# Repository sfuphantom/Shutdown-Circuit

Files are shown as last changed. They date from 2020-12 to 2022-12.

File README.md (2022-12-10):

# Shutdown-Circuit
The Shutdown Circuit (SDC), now more commonly known as the high voltage (HV) and low voltage (LV) shutdown boards (SDBs), controls shutting down the vehicle in the occurance of a fault. Accordingly, the HV SDB is located in the HV system, and the LV SDB is in the LV system where if a fault were detected in either system then the vehicle turns off completely.

We use JLC PCB for supplying great PCBs in a timely manner:
https://jlcpcb.com/?from=RAT

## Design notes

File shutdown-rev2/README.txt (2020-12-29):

Additional Altium libraries required:

\Phantom-Library\LEDs.SchLib        # for LEDs
\Phantom-Library\Diodes.SchLib      # for diodes
\Phantom-Library\Misc.SchLib        # for testpoints
\Phantom-Library\Connectors.SchLib  # for 1x8 connector
\Phantom-Library\PCBLib             # for all generic footprints (resistors, capacitors, SOT23-3, etc.)

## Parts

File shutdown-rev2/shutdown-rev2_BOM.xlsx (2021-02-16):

Description | Designator | LibRef | Quantity
CAP CER 0.1UF 50V X7R 0603 | C1, C2, C3, C4, C5, C6, C7, C8, C9, C10, C11 | CL10B104KB8NNNL | 11
CAP CER 15UF 6.3V X5R 0603 | C12 | C1608X5R0J156M080AC | 1
LED YELLOW CLEAR 0603 SMD | D1 | LED-Yellow | 1
DIODE GEN PURP 600V 5A SMB | D2, D4, D6, D8 | Diode-600V-5A | 4
LED RED CLEAR 0603 SMD | D3, D5, D7, D9 | LED-Red-Bright | 4
CONN HEADER VERT 2POS 2.54MM | JP1, JP2, JP3, JP4 | 2PIN-TEST | 4
General Purpose Relay, Osa Series, Power, Non Latching, Dpst-No, 12 Vdc, 3 A Rohs Compliant: Yes | K1, K2, K3, K4 | 5-1419124-6 | 4
CONN HEADER VERT 2POS 5.7MM, 12-16AWG | M1 | 2002411112 | 1
4 PIN HDR, 3MM PITCH, 18-30 AWG | M2, M4 | 0436500428 | 2
CONN HEADER VERT 5POS 3MM | M3 | 0436500528 | 1
CONN HEADER R/A 8POS 2.54MM | M5 | 8PIN | 1
MOSFET 2N-CH 60V 0.25A SOT363 | Q1, Q3, Q5, Q7 | DMN63D1LDW | 4
P Channel MOSFET, -130 mA, -50 V, 1.2 ohm, -5 V, -1.7 V | Q2, Q4, Q6, Q8 | BSS84 | 4
MOSFET N-CH 50V 200MA SOT-23 | Q9 | BSS138LT3G | 1
RES SMD 240 OHM 5% 1/4W 0603 | R1, R3, R5, R8, R10 | ESR03EZPJ241 | 5
RES SMD 10K OHM 1% 1/10W 0603 | R2, R4, R9, R11, R16 | CRCW060310K0FKEA | 5
RES SMD 1K OHM 1% 1/10W 0603, RES SMD 240 OHM 5% 1/4W 0603 | R6, R7, R12, R17, R25 | CRCW06031K00FKEA, ESR03EZPJ241 | 5
RES 3K OHM 5% 1/10W 0603 | R13, R15, R20 | RMCF0603JT3K00 | 3
RES 9.1K OHM 1% 1/10W 0603 | R14, R18 | RMCF0603FT9K10 | 2
RES 7.5K OHM 1% 1/8W 0603 | R19 | RNCP0603FTD7K50 | 1
RES SMD 1.3K OHM 1% 1/8W 0603 | R21 | MCT06030C1301FP500 | 1
RES SMD 2.2K OHM 1% 1/10W 0603 | R22 | RC0603FR-072K2L | 1
RES SMD 33K OHM 1% 1/10W 0603 | R23 | RC0603FR-0733KL | 1
RES SMD 499 OHM 0.1% 1/10W 0603 | R24 | ERA-3AEB4990V | 1
RES SMD 2K OHM 0.1% 1/10W 0603 | R26 | ERA-3AEB202V | 1
Single layer pad TP | TP1, TP2, TP3 | Testpoint2 | 3
TVS DIODE ARRAY 12VWM SOT23-3 | U1, U4 | AQ12-02HTG | 2
TVS DIODE 5V 14.5V SOD323 | U2 | AQ05C-01FTG | 1
TVS DIODE ARRAY 5VWM SOT23-3 | U3, U6 | AQ05-02HTG | 2
TVS DIODE 12V 23V SOD323 | U5, U7 | AQ12C-01FTG | 2
IC COMPAR PWR RRI DL PP 8VSSOP | U8, U14 | TLV3202AIDGK | 2
IC GATE OR 2CH 2-INP US8 | U9 | NL27WZ32USGOSCT-ND | 1
Dual 2-Input Positive-AND Gate | U10 | SN74LVC2G08DCUT | 1
The SN74AHC1G04 contains one inverter gate. The device performs the Boolean function Y = A bar. | U11, U13 | SN74AHC1G04DCK | 2
Comparator Single R-R I/P 5.5V 5-Pin SC-70 T/R | U12 | TLV3201AIDCKR | 1

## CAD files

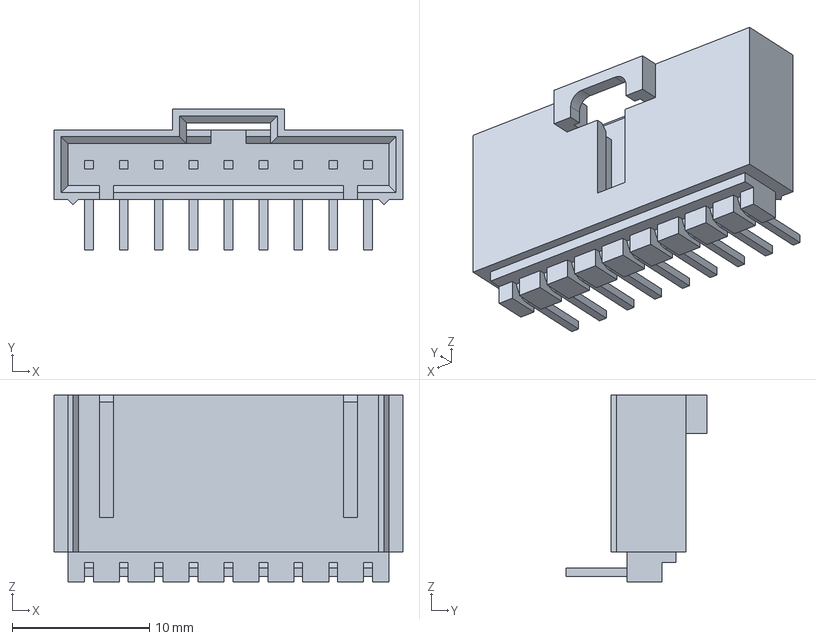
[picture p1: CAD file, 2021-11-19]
HV SDB/705530113.stp
25.4 x 10.3 x 13.6 mm

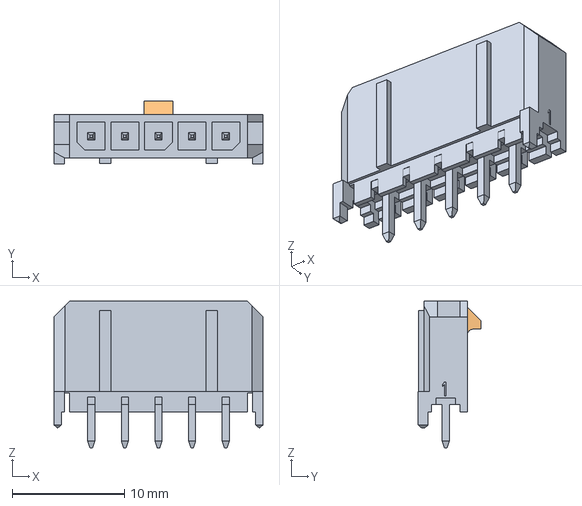
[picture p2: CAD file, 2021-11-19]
LV SDB/436500528.stp
18.6 x 5.61 x 13.1 mm

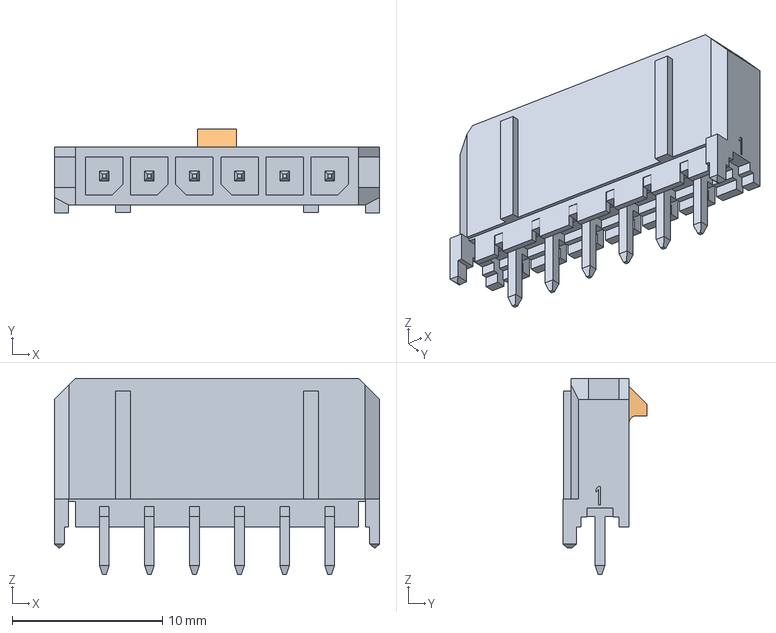
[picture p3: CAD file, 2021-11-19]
LV SDB/436500628.stp
21.6 x 5.61 x 13.1 mm

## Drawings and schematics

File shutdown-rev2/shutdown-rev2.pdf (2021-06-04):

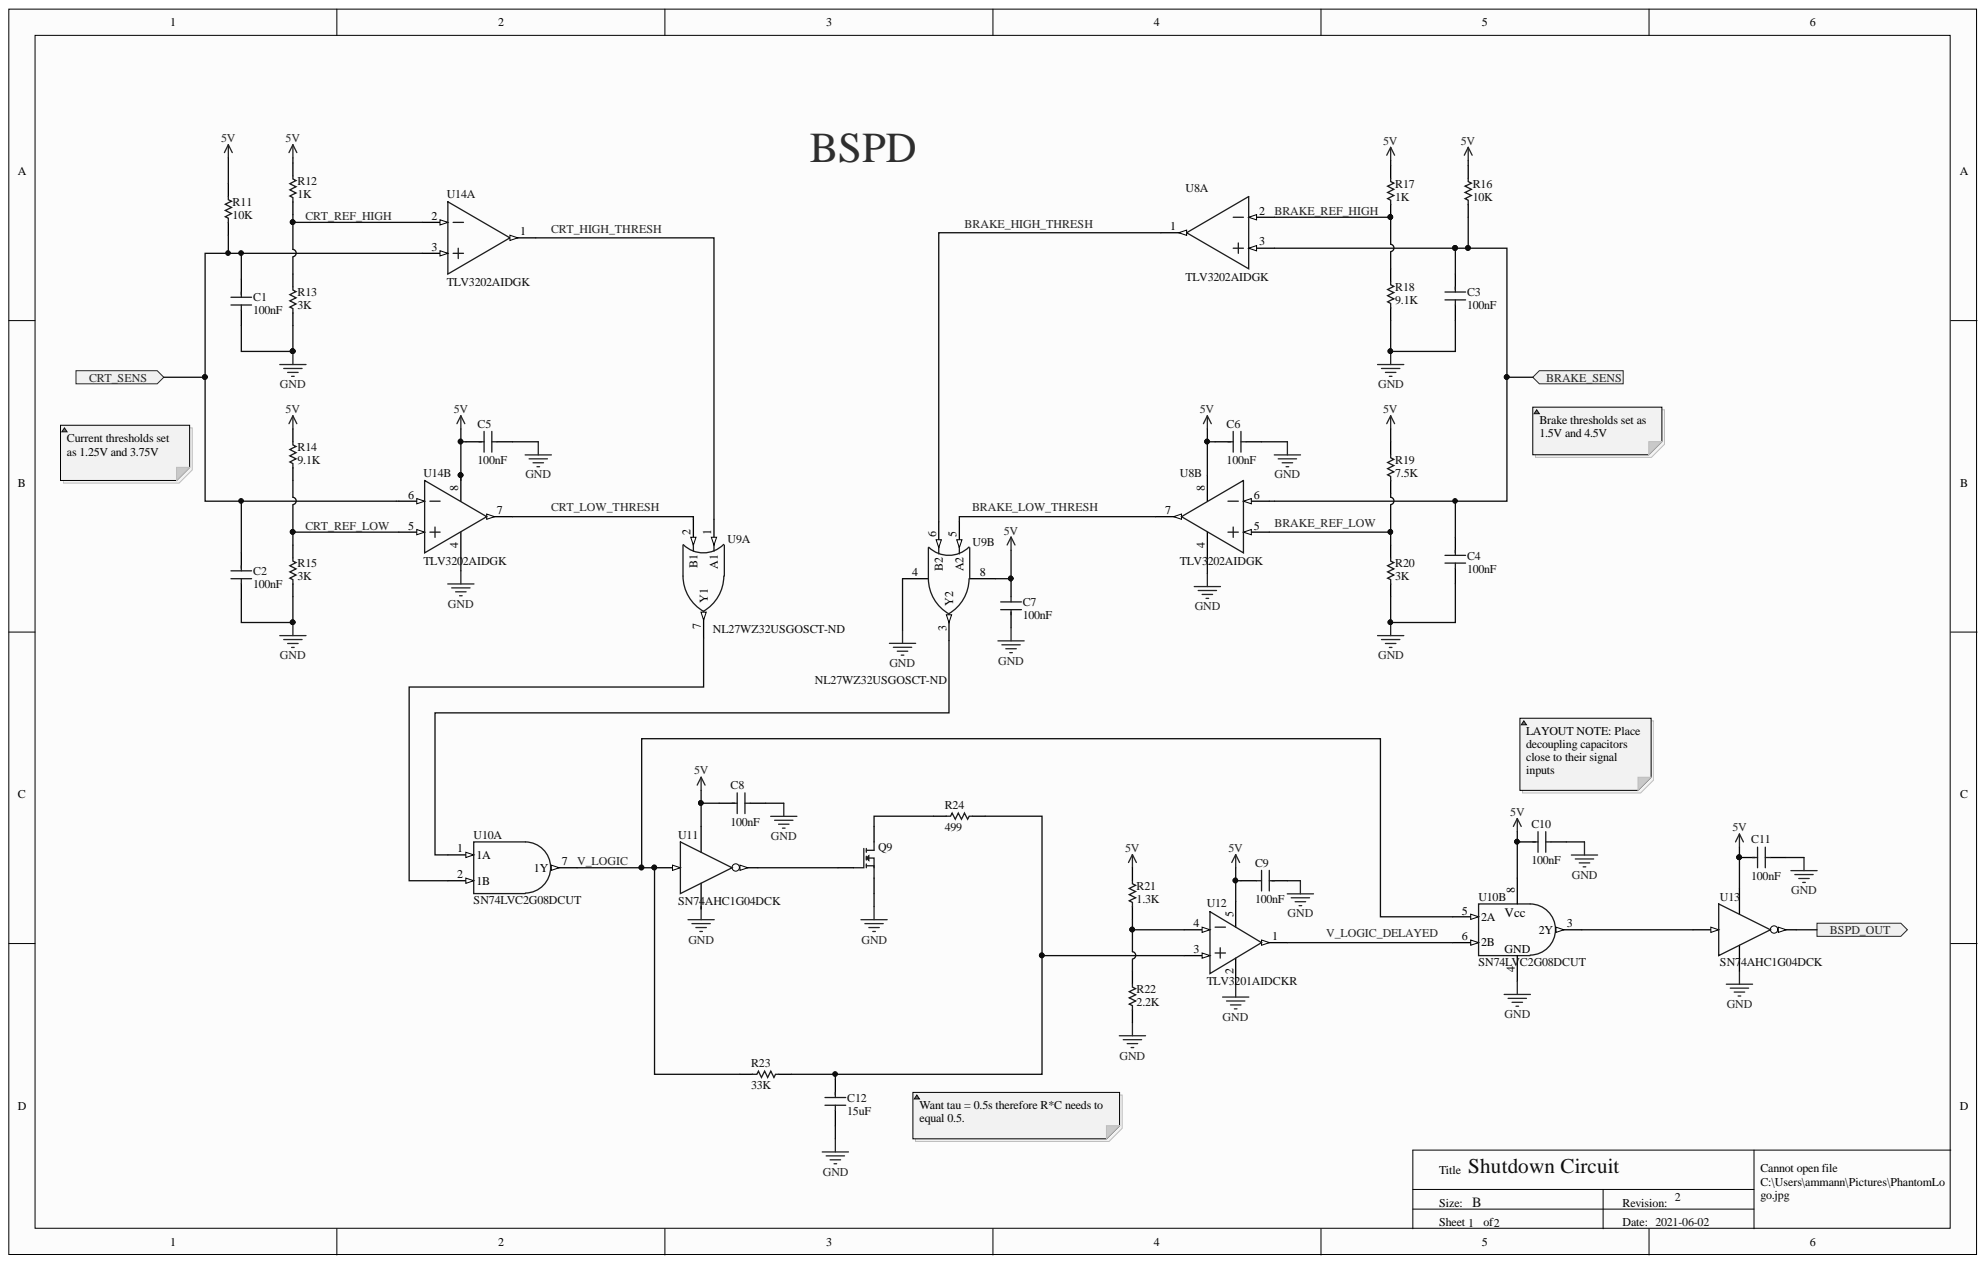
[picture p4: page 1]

1.5V and 4.5V Current thresholds set
as 1.25V and 3.75V

Brake thresholds set as

NL27WZ32USGOSCT-ND

LAYOUT NOTE: Place
decoupling capacitors
close to their signal
inputs

Want tau = 0.5s therefore R*C needs to
equal 0.5.

Cannot open file
C:\Users\ammann\Pictures\PhantomLo
go.jpg

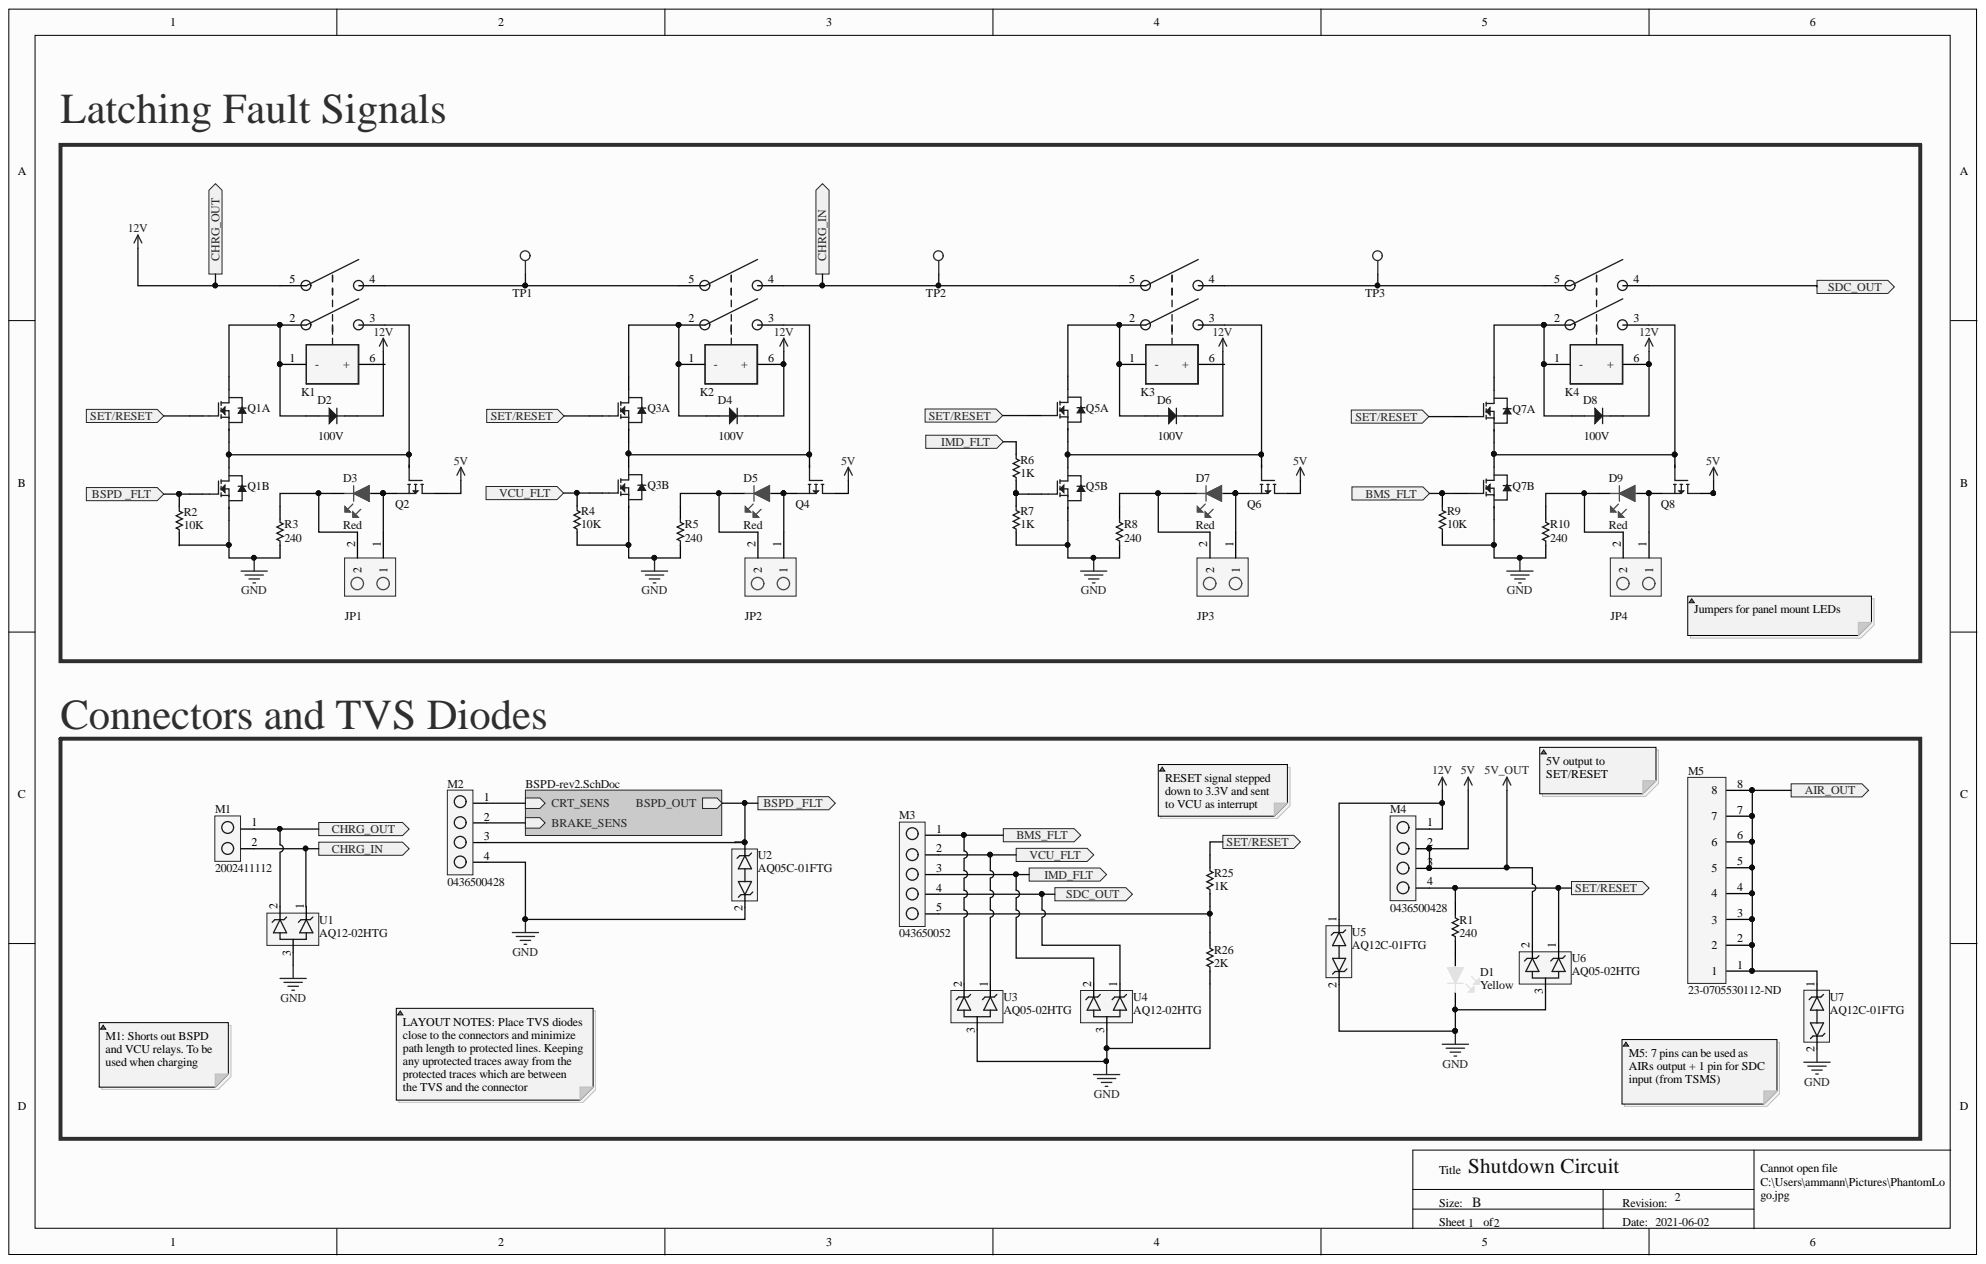
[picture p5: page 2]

Jumpers for panel mount LEDs

Connectors and TVS Diodes

RESET signal stepped
down to 3.3V and sent
to VCU as interrupt

LAYOUT NOTES: Place TVS diodes
close to the connectors and minimize
path length to protected lines. Keeping
any uprotected traces away from the
protected traces which are between
the TVS and the connector

M1: Shorts out BSPD
and VCU relays. To be
used when charging

M5: 7 pins can be used as
AIRs output + 1 pin for SDC
input (from TSMS)

Cannot open file
C:\Users\ammann\Pictures\PhantomLo
go.jpg

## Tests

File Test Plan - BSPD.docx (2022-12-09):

BSPD on Shutdown Rev 2 Test Plan

Project Revision 1 / Software Version

Nina Lin

## Summary

The Brake System Plausibility Device (BSPD) is a linear and logic system used to detect a fault with the brake system in different scenarios which will trigger the Low Voltage (LV) shutdown circuit of the tractive system (turn on/activate/ to shutdown). The integration of the BSPD with the shutdown circuit onto a single PCB allows the BSPD to monitor the major fault relays and send the corresponding signals to the shutdown system to prevent operation during unsafe/ major faulting scenarios. The 4 major faults monitored by the shutdown circuit are the BSPD_FLT, BMS_FLT, VCU_FLT, and IMD_FLT. Each fault is triggered by another set of signals indicating faults within the tractive system. We are looking at the BSPD_FLT.

1.) The BSPD takes the CRT_SENS input signal and compares it with a CRT_REF_HIGH(3.75V) and CRT_REF_LOW(1.25V) signal.

a. When the sensor signal is compared with the reference signal CRT_REF_HIGH, it will output the CRT_SENS signal (as HIGH-1) if the sensor voltage is the larger signal and CRT_REF_HIGH (as LOW-0) if the sensor voltage is smaller than the reference signal. The output is now the CRT_HIGH_THRES signal. Ideally, we want this signal to be a LOW-0.

b. When the sensor signal is compared with the reference signal CRT_REF_LOW, it will output the CRT_REF_LOW (as HIGH-1) if the sensor signal is less than reference and output the CRT_SENS (as LOW-0) if the sensor signal is larger than the reference. The output is now the CRT_LOW_THRES signal. Ideally, we want this signal to be a LOW-0.

c. The CRT_HIGH_THRES and CRT_LOW_THRES signals pass through an OR gate which will only output a LOW-0 signal if both input signals are LOW-0. All other conditions mean that the current sensor signal is not within threshold voltage and will result in a HIGH-1 signal output. Hence, we want this signal to be a LOW-0.

2.) The BSPD takes the BRAKE_SENS input signal and compares it with a BRAKE_REF_HIGH(4.5V) and BRAKE _REF_LOW(1.5V) signal.

a. When the sensor signal is compared with the reference signal BRAKE _REF_HIGH, it will output the BRAKE _SENS signal (as HIGH-1) if the sensor voltage is the larger signal and BRAKE _REF_HIGH (as LOW-0) if the sensor voltage is smaller than the reference signal. The output is now the BRAKE _HIGH_THRES signal. Ideally, we want this signal to be a LOW-0.

b. When the sensor signal is compared with the reference signal BRAKE _REF_LOW, it will output the BRAKE _REF_LOW (as HIGH-1) if the sensor signal is less than reference and output the BRAKE _SENS (as LOW-0) if the sensor signal is larger than the reference. The output is now the BRAKE _LOW_THRES signal. Ideally, we want this signal to be a LOW-0.

c. The BRAKE _HIGH_THRES and BRAKE _LOW_THRES signals pass through an OR gate which will only output a LOW-0 signal if both input signals are LOW-0. All other conditions mean that the current sensor signal is not within threshold voltage and will result in a HIGH-1 signal output. Hence, we want this signal to be a LOW-0.

3.) The output signals from 1c and 2c pass through an AND logic gate which will output a HIGH-1 signal if neither current nor brake sensor signals meet threshold voltages. A LOW-0 signal output will result if both current and sensor signals meet threshold values, or if either sensor signal meet threshold values. The output is now the V LOGIC signal. LOW-0 desired.

4.) The V LOGIC output goes through an time delay circuit by approximately 40ns (datasheet) which can be thought of as the previous signal called V LOGIC DELAYED.

5.) A logic AND gate compares the V LOGIC (real time signal) with the V LOGIC DELAYED (previous signal) reading. If both signals are HIGH-1, this means that the current and brake sensor signals are not within threshold for an extend time (not instantaneous) so the logic gate will output a HIGH-1 voltage signal. If both signals are LOW-0, the continuous check on the current and brake sensors meet threshold values and the output will be a LOW-0. LOW-0 desired.

6.) An inverter circuit is used output the BSPD_OUT signal. If the input is a HIGH-1 then the BSPD_OUT will be ACTIVE LOW, an indication of a fault. This will open the switch and send a fault signal and will need to be reset. If the input is LOW-0 then the BSPD_OUT will be ACTIVE HIGH, an indication that the current and brakes sensors meet safe operating conditions and no fault signal sent.

ACTIVE HIGH | Gate Signal | Switch(Set/Reset) Close | No fault signal
ACTIVE LOW | No Gate Signal | Switch(Set/Reset) Open | Fault Signal Sent

## Project Pictures

## Summary of Test

This test evaluates the operation of the BSPD circuit in outputting a constant active high/gate signal for current and brake sensor values within threshold and outputting an active low signal for current and/or brake sensor values falling out of the threshold ranges. Scenarios of current input and brake inputs being within range are tested for a gate signal output from the BSPD circuit. Scenarios of current and brake sensor voltages falling out of range (too low or too high) are tested for no gate signal output from the BSPD circuit.

## Test Being Performed

### Equipment/Lab Materials

2 Power supply (2 channels)

Breadboard (equivalent to the pcb)

LED (1) – 3V operating range

10 Ohm resistor (minimum value)

Wires/Alligator clips

Multimeter(For reading Voltage)

Soldering iron (maybe??)

Test headers(male PCB headers)

Precautions:

### Procedure (Test Cases)

General Procedure:

1.) Construct simple LED-resistor circuit using BSPD output as the input. R = 10Ohm, Vs = BSPD_OUT

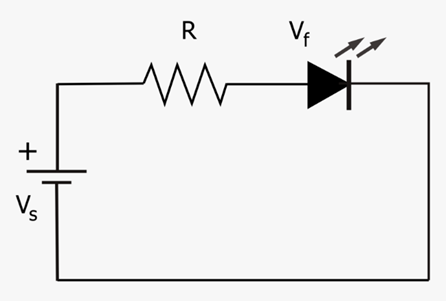
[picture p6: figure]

2.) Connect CH1 of power supply to the CRT_SENS to simulate current sensor input.

3.) Connect CH2 of power supply to BRAKE_SENS to simulate brake sensor input.

4.) Ground everything.

Case 1: Current Sensor and Brake Sensor within Range

1.) Set CH1 voltage to 1.6V

2.) Set CH2 voltage to 3.0V

3.) Measure BSPD_OUT voltage and record it. Record LED observations.

4.) Repeat step 1 using 1.5V, 1.7V, 1.9V, 2.1V, 2.3V, 2.5V, 2.7V, 2.9V, 3.1V, 3.3V, 3.5V, and 3.7V respectively. Keep CH2 constant.

5.) Set CH2 voltage to 1.3V

6.) Set CH1 voltage to 2.5V

7.) Measure BSPD_OUT voltage and record it. Record LED observations.

8.) Repeat step 5 using 1.8V, 2.0V, 2.2V, 2.4V, 2.6V, 2.8V, 3.0V, 3.2V, and 3.4V respectively. Keep CH1 constant.

Case 2: Current Sensor within Range, Brake Sensor out of Range (too low)

1.) Set CH2 voltage to 1.5V

2.) Set CH1 voltage to 2.5V

3.) Measure BSPD_OUT voltage and record it. Record LED observations.

4.) Repeat step 5 using 1.4V, 1.2V, 1.0V, 0.8V, 0.6V, 0.4V, 0.2V and 0.0V respectively. Keep CH1 constant.

Case 3: Current Sensor within Range, Brake Sensor out of Range (too high)

1.) Set CH2 voltage to 4.5V

2.) Set CH1 voltage to 2.5V

3.) Measure BSPD_OUT voltage and record it. Record LED observations.

4.) Repeat step 5 using 4.6V, 4.7V, 4.8V, 4.9V, 5.0V, 5.1V, 5.2V, and 5.3V respectively. Keep CH1 constant.

Case 4: Brake Sensor within Range, Current Sensor out of Range (too low)

1.) Set CH1 voltage to 1.25V

2.) Set CH2 voltage to 3.0V

3.) Measure BSPD_OUT voltage and record it. Record LED observations.

4.) Repeat step 1 using 1.2V, 1.0V, 0.8V, 0.6V, 0.4V, 0.2V, 0.1V, and 0V respectively. Keep CH2 constant.

Case 5: Brake Sensor within Range, Current Sensor out of Range (too high)

1.) Set CH1 voltage to 3.75V

2.) Set CH2 voltage to 3.0V

3.) Measure BSPD_OUT voltage and record it. Record LED observations.

4.) Repeat step 1 using 3.8V, 4.0V, 4.2V, 4.4V, 4.6V, 4.8V, and 5.0V respectively. Keep CH2 constant.

Case 6: Current Sensor (high) and Brake Sensor out of range (high)

1.) Set CH1 voltage to 3.75V and Set CH2 voltage to 4.5V. Measure and record BSPD_OUT and LED observations.

2.) Set CH1 voltage to 3.8V and Set CH2 voltage to 4.6V. Measure and record BSPD_OUT and LED observations.

3.) Set CH1 voltage to 4.0V and Set CH2 voltage to 4.7V. Measure and record BSPD_OUT and LED observations.

4.) Set CH1 voltage to 4.2V and Set CH2 voltage to 4.8V. Measure and record BSPD_OUT and LED observations.

5.) Set CH1 voltage to 4.4V and Set CH2 voltage to 4.9V. Measure and record BSPD_OUT and LED observations.

6.) Set CH1 voltage to 4.6V and Set CH2 voltage to 5.0V. Measure and record BSPD_OUT and LED observations.

Case 7: Current Sensor (high) and Brake Sensor out of range (low)

1.) Set CH1 voltage to 3.75V and Set CH2 voltage to 1.5V. Measure and record BSPD_OUT and LED observations.

2.) Set CH1 voltage to 3.8V and Set CH2 voltage to 1.4V. Measure and record BSPD_OUT and LED observations.

3.) Set CH1 voltage to 4.0V and Set CH2 voltage to 1.2V. Measure and record BSPD_OUT and LED observations.

4.) Set CH1 voltage to 4.2V and Set CH2 voltage to 1.0V. Measure and record BSPD_OUT and LED observations.

5.) Set CH1 voltage to 4.4V and Set CH2 voltage to 0.8V. Measure and record BSPD_OUT and LED observations.

6.) Set CH1 voltage to 4.6V and Set CH2 voltage to 0.6V. Measure and record BSPD_OUT and LED observations.

Case 8: Current Sensor (low) and Brake Sensor out of range (high)

1.) Set CH1 voltage to 1.25V and Set CH2 voltage to 4.5V. Measure and record BSPD_OUT and LED observations.

2.) Set CH1 voltage to 1.2V and Set CH2 voltage to 4.6V. Measure and record BSPD_OUT and LED observations.

3.) Set CH1 voltage to 1.0V and Set CH2 voltage to 4.7V. Measure and record BSPD_OUT and LED observations.

4.) Set CH1 voltage to 0.8V and Set CH2 voltage to 4.8V. Measure and record BSPD_OUT and LED observations.

5.) Set CH1 voltage to 0.6V and Set CH2 voltage to 4.9V. Measure and record BSPD_OUT and LED observations.

6.) Set CH1 voltage to 0.4V and Set CH2 voltage to 5.0V. Measure and record BSPD_OUT and LED observations.

Case 9: Current Sensor (low) and Brake Sensor out of range (low)

1.) Set CH1 voltage to 1.25V and Set CH2 voltage to 1.5V. Measure and record BSPD_OUT and LED observations.

2.) Set CH1 voltage to 1.2V and Set CH2 voltage to 1.4V. Measure and record BSPD_OUT and LED observations.

3.) Set CH1 voltage to 1.0V and Set CH2 voltage to 1.2V. Measure and record BSPD_OUT and LED observations.

4.) Set CH1 voltage to 0.8V and Set CH2 voltage to 1.0V. Measure and record BSPD_OUT and LED observations.

5.) Set CH1 voltage to 0.6V and Set CH2 voltage to 0.8V. Measure and record BSPD_OUT and LED observations.

6.) Set CH1 voltage to 0.4V and Set CH2 voltage to 0.6V. Measure and record BSPD_OUT and LED observations.

### Results

Provide any and all qualitative and quantitative results obtained by the test. Any results, tables, graphs should be shown here as well as pictures of the test being performed.

### Functionality Check

Expected Results:

| Fault | BSPD_OUT Voltage Reading | LED Observation
Case 1 | No Fault | Between 3.5 to 5.5V | LED ON
Case 2 | No Fault | Between 3.5 to 5.5V | LED ON
Case 3 | No Fault | Between 3.5 to 5.5V | LED ON
Case 4 | No Fault | Between 3.5 to 5.5V | LED ON
Case 5 | No Fault | Between 3.5 to 5.5V | LED ON
Case 6 | Fault | Between 0 to 1V | LED OFF (or very dim)
Case 7 | Fault | Between 0 to 1V | LED OFF
Case 8 | Fault | Between 0 to 1V | LED OFF
Case 9 | Fault | Between 0 to 1V | LED OFF

Table with all the voltages they need to firmware team to program the

***talk to firmware team to see what they need

Whoever working on BSPD and accelerator and brake pedal and ensure the test can provide them

Make sure BSPD works (validation) and Ensure it can properly integrate with software (and the hardware)

1. Assemble everything in a testable manner
2. Headers wires power supply connection
3. Bare table with results record on each case(excel or on test plan)
4. Have meeting (include Andrei)

Team Phantom

<Project Name> Test Plan

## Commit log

2020-11-19 SDC rev2 with BSPD
    [BSPD-rev2.SchDoc, BSPD.SchLib, SDC-rev2.SchDoc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]
2020-11-26 Rev 2 schematic changes
    [BSPD-rev2.SchDoc, SDC-rev2.SchDoc, SDC.SchLib]
2020-11-28 Rev 2: Schematic changes after schematic review
    [BSPD-rev2.SchDoc, BSPD.PcbLib, BSPD.SchLib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]
2020-11-28 Updated designators and attached footprints to symbols
    Updated BSPD.SchLib
    Updated designators and attached footprints to symbols
    [BSPD-rev2.SchDoc, BSPD.SchLib, SDC-rev2.SchDoc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]
2020-12-07 Completed SDC-BSPD rev 2 PCB
    Fix
    Completed SDC-BSPD rev 2 PCB
    [BSPD-rev2.SchDoc, BSPD.PcbLib, SDC-BSPD-rev2.PcbDoc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]
2020-12-29 Revisions to SDC-BSPD rev 2 PCB
    Changing CHARGING conn to 2x1
    Revisions to SDC-BSPD rev 2 PCB
    [BSPD-rev2.SchDoc, OLD_SDC-BSPD-rev2.PcbDoc, SDC-BSPD-rev2.PcbDoc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]
2020-12-30 Revisions to SDC-BSPD rev 2 PCB after 2nd board review
    [SDC-BSPD-rev2.PcbDoc, SDC.PcbLib, shutdown-rev2.PrjPCB]
2021-01-25 Added 3.3V SET/RESET output for VCU to M3
    [SDC-BSPD-rev2.PcbDoc, SDC-rev2.SchDoc, SDC.PcbLib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]
2021-02-16 Added BOM
    [BSPD-rev2.SchDoc, BSPD.SchLib, SDC-rev2.SchDoc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]
2021-06-04 changed LED logic
    [SDC-rev2.SchDoc, SDC.SchLib, shutdown-rev2.PrjPCB]
2021-06-04 add new LED logic to PCB, removed TVS
    [BSPD-rev2.SchDoc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]
2021-06-12 generated gerbers and BOM
    [SDC-BSPD-rev3.xlsx, shutdown-rev2.PrjPCB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]
2021-06-14 Reprint SDC with lathching indicator lights
    [SDC-BSPD-rev2.PcbDoc, SDC-BSPD-rev3.xlsx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]
2021-09-12 Added and editted the HV SDB schematic.
    [hvSdb-rev0.PrjPCB, hvSdbSchLib.SchLib, hvSdbSchematic.SchDoc]
2021-09-12 Added a note stating the uncertainties of the schematic design.
2021-09-13 Revised the connectors.
    [hvSdbSchLib.SchLib, hvSdbSchematic.SchDoc]
2021-09-15 Added PCB design and PCB library to the HV SDB
    [hvSdb-rev0.PrjPCB, hvSdbPCB.PcbDoc, hvSdbPcbLib.PcbLib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]
2021-09-21 Added HV SDB schematic to the PCB layout
    [hvSdbPCB.PcbDoc, hvSdbPcbLib.PcbLib, hvSdbSchLib.SchLib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]
2021-09-22 Finished Rev 0 of HV SDB, revised schematic, libraries, and editted PCB layout
    [hvSdb-rev0.PrjPCB, hvSdbPCB.PcbDoc, hvSdbPcbLib.PcbLib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]
2021-10-20 Revised Rev 0 of the HV SDB by creating cleaner traces, removing bottlenecks, moving around commponent for more efficient traces, etc.
    [hvSdbPCB.PcbDoc, hvSdbPcbLib.PcbLib, hvSdbSchLib.SchLib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]
2021-11-19 Revised HV SDB
    [436500528.stp, 436500628.stp, 705530113.stp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]
2021-11-22 Finished revision 0 of LV SDB
    [lvSdbPcb.PcbDoc, lvSdbSchematic.SchDoc]
